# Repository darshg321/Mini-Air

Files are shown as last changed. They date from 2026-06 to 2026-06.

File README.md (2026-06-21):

# Mini-Air

Mini-Air is a DIY FPV drone!
it features:
- a custom flight controller supporting Betaflight
- an ESC supporting Bluejay firmware
- ELRS protocol
- an analog camera
- GPS

the custom flight controller has an on-board OSD, IMU, Barometer, and SPI Flash

i made this project to learn how flight controllers and drones work, and because i want to fly a cool fpv drone. the project is optimized to support the features of all the latest fpv software available. all components are analog to reduce latency, and because 480p drone video with osd in general is really aesthetic. with a 2s lipo and a 2-inch propellers, it leans heavily towards speed rather than range or flight time. the vtx, gps, reciever, and esc are all modular, and so can be swapped with different parts if needed. note that the CAD is simplified to just show the rough connection, i am using a bought frame which will allow for screwing in components.

## Poster (Zine)
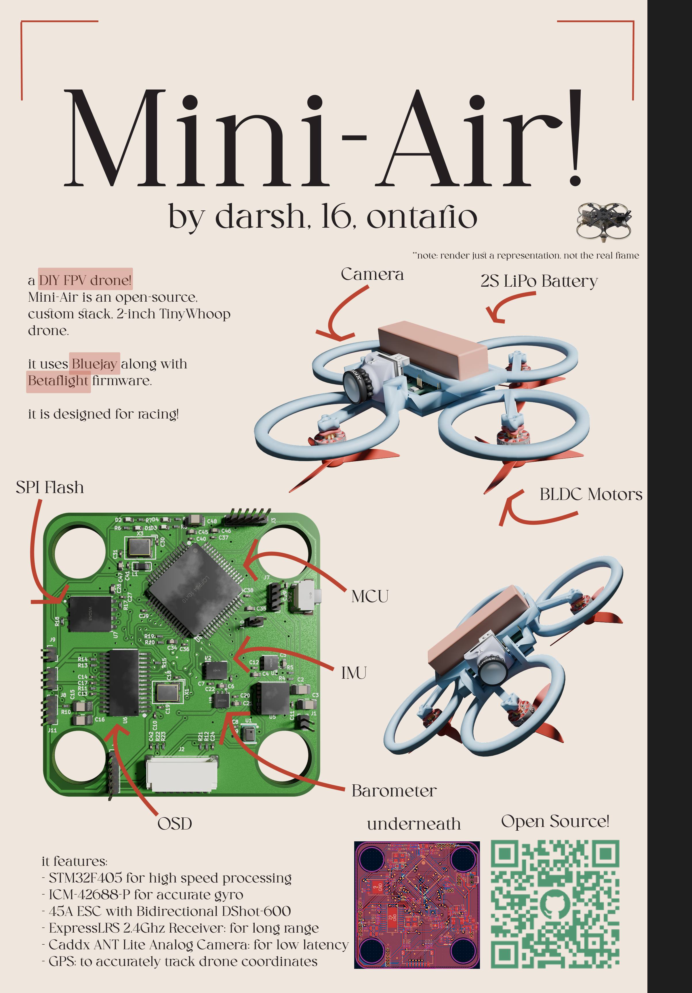
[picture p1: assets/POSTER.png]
poster


## Flight Controller Render
pcb render

## CAD Render
cad render

## PCB
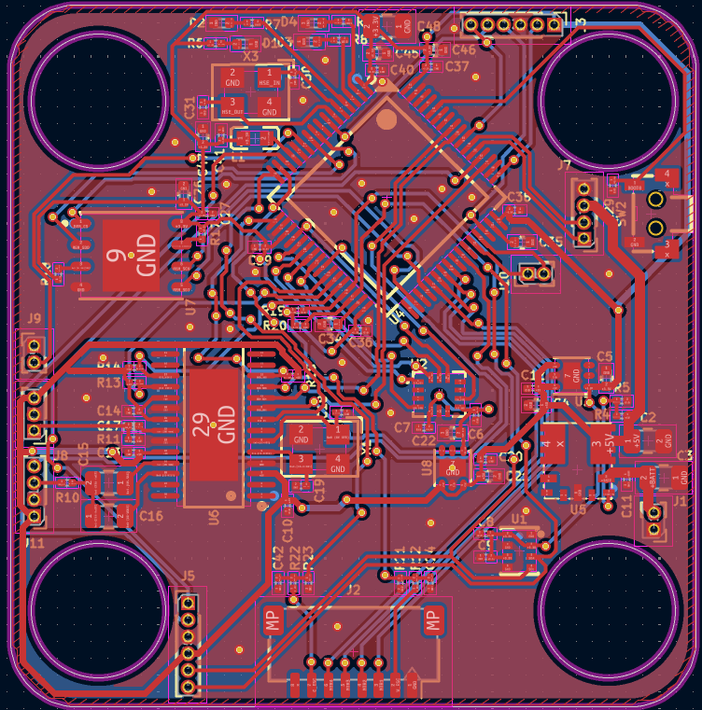
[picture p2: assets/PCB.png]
pcb


## Schematic
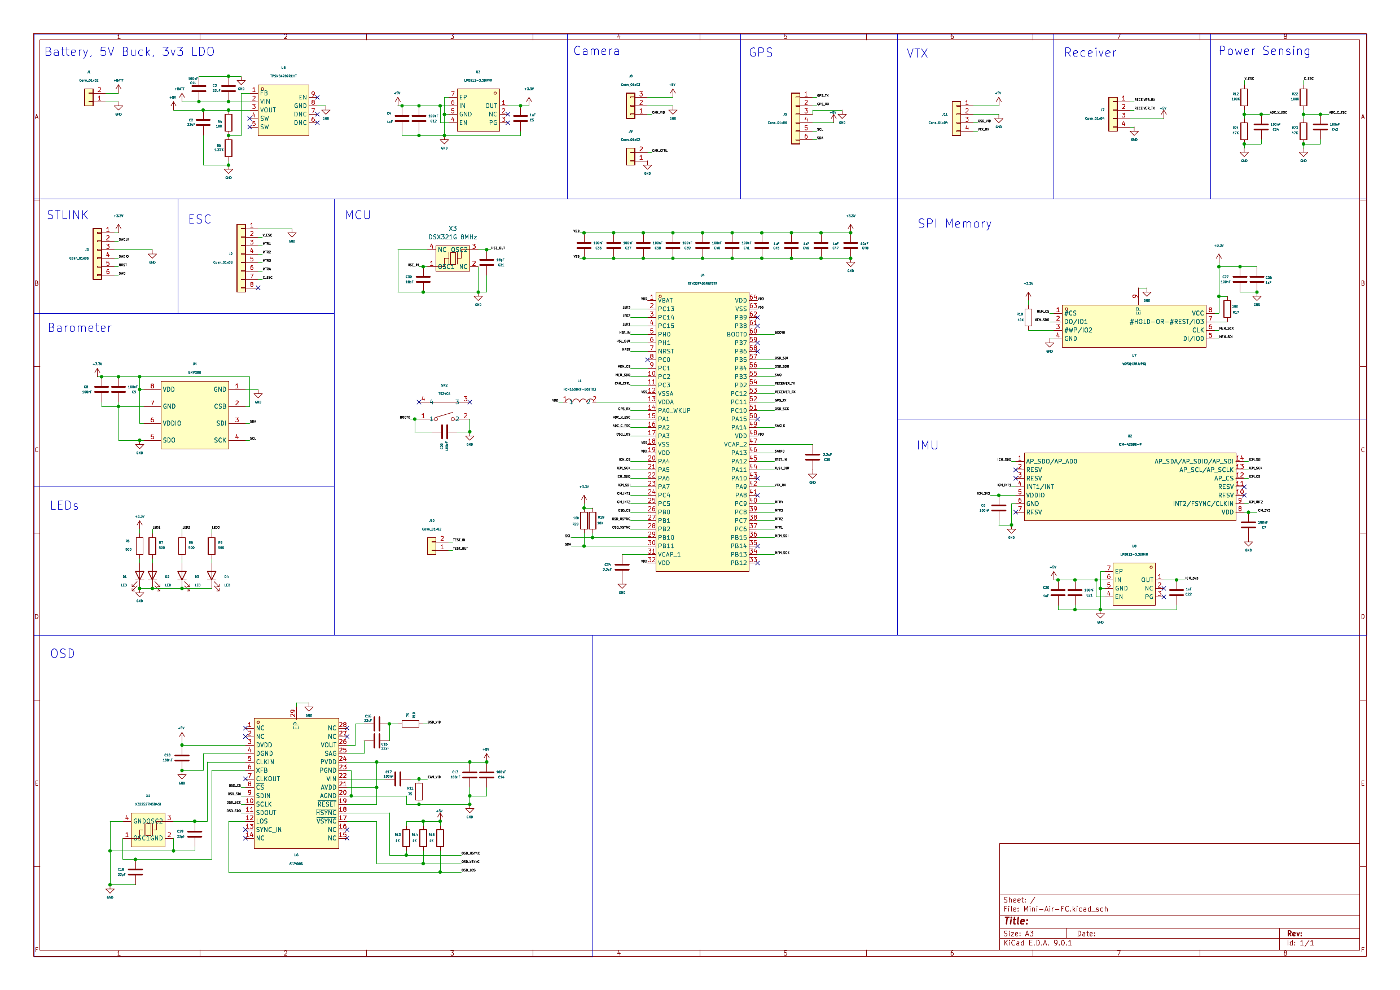
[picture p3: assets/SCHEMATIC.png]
schematic


## CAD
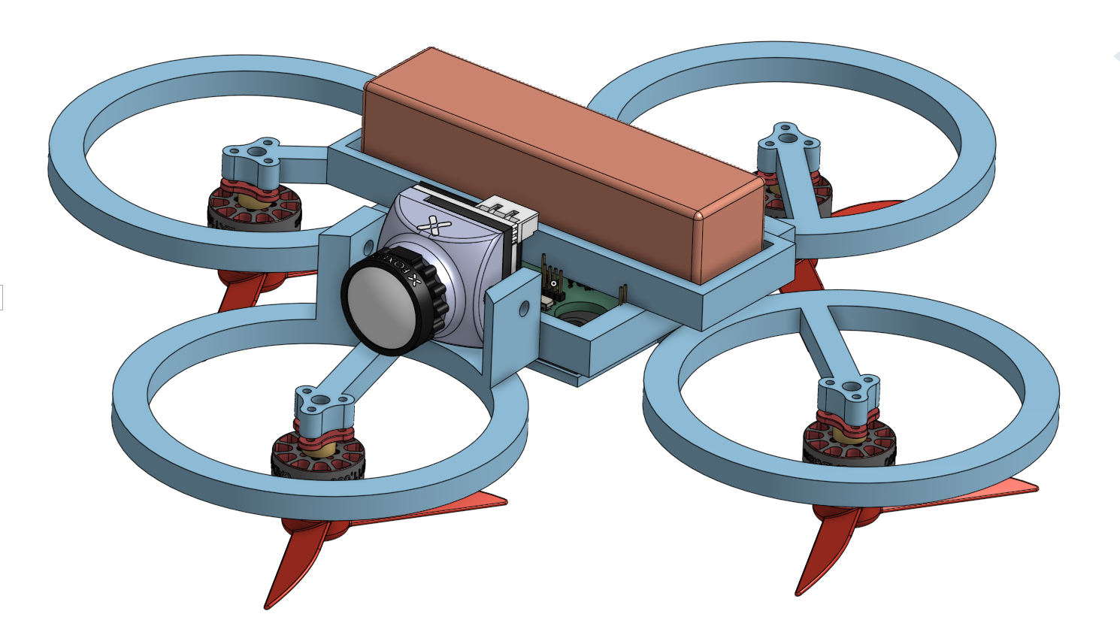
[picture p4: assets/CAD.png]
cad

https://cad.onshape.com/documents/986fb99af7814b930792b89c/w/8ba981f62ca8b18288746bfa/e/dd69b1ef7cccc17bc086fed8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

## Assembly:

1. mount ESC and FC to frame and screw in
2. mount propeller to motor and screw in to frame
3. solder camera, vtx, gps, reciever to flight controller
4. mount camera to front of frame, screw in other components to the back
5. flash betaflight firmware by connecting to FC with a STLINK
6. connect battery and radio controller
7. fly!

## BOM

|Item: |Link: |Price (CAD):|FIELD4|FIELD5 |Weight (g)|
|---|---|---|---|---|---|
|FC PCB | |2.83 | | |3.9 |
|FC PCBA | |236.5 | | | |
|Frame |https://epicfpv.ca/products/hglrc-talon-frame-black |45.31 | | |46 |
|AneegFpv 45A ESC |https://www.aliexpress.com/item/1005009952151526.html |32.99 | | |13 |
|4x HappyModel EX1103S 1103 7000KV |https://www.aliexpress.com/item/1005006105578345.html |44.59 | | |15.2 |
|Propellers |https://www.aliexpress.com/item/1005006966517627.html |6.49 | | |3.52 |
|CADDX Ant FPV Lite Camera |https://www.aliexpress.com/item/1005009014299964.html |19.87 | | |2 |
|Zeus nano 350mW VTX |https://www.aliexpress.com/item/1005008558004179.html |35.58 | | |2.4 |
|Foxeer Lollipop 3 Micro Omni V4 RHCP Antenna|https://www.aliexpress.com/item/4001191873858.html |16.89 | | |4.7 |
|HappyModel 2.4G ELRS EP2 Reciever |https://www.aliexpress.com/item/1005009851731060.html |19.18 | | |0.41 |
|NewBeeDrone M10Q Micro GPS Module |https://newbeedrone.com/products/newbeedrone-m10q-micro-gps-module-with-compass|27.80 | | |2.61 |
|LiteRadio 2 ELRS |https://www.aliexpress.com/item/1005011890268150.html |31.18 | | | |
|x4 2S 450mAh 80C lipo battery |https://www.aliexpress.com/item/1005006138925891.html |37.99 | | |30 |
| | | | | | |
| |Total USD |401.18 | |Weight:|123.74 |

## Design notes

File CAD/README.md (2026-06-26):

**note**: the cad is NOT a frame but rather just a representation of kinda what the drone will look like. the real frame is in the BOM

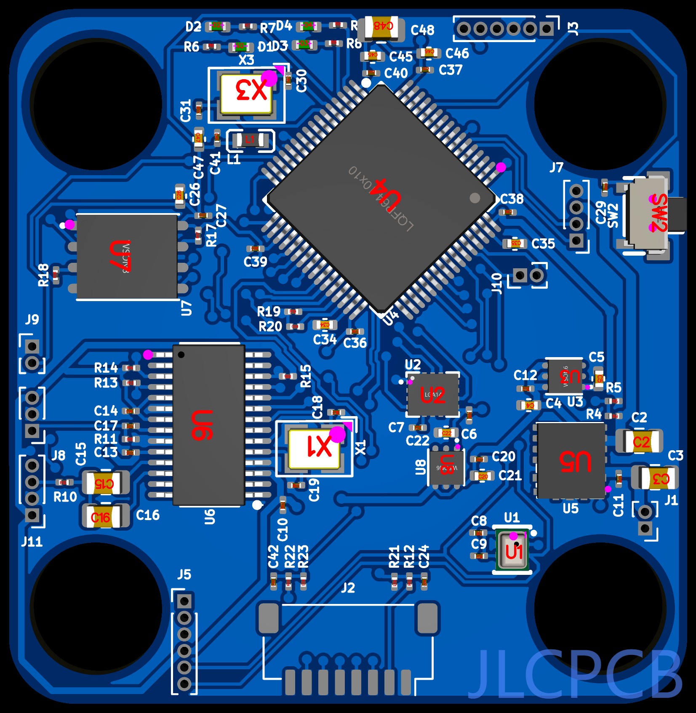
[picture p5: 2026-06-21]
assets/PCB_JLC.png

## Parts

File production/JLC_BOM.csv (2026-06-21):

JLCPCB BOM Tool - BOM Matching
BOM name：production_bom-JLCPCB Assembly Order.xlsx |  |  | Download Time：2026-06-21 03:50:59 |  |  |  | * Our matching results are updated in real-time, but stock and prices may change. If it's been over 24 hours, please re-match before placing your order.
PCB Assembled Qty：5 |  |  | Est. Total Price：83.5555
Your BOM |  |  |  |  | Matched Parts |  |  |  |  |  |  | Order Information
Top Designator | Bottom Designator | Comment | Footprint | JLCPCB Part # | Matches | Part # | Manufacturer | Footprint | Description | Category | Warning | JLCPCB Part # | Product link | Lib Type | Qty | Source | Total Price ($)
C10,C11,C12,C13,C14,C17,C21,C24,C27,C29,C36,C37,C38,C39,C40,C41,C42,C6,C7,C8,C9 |  | 100nF | 0201 |  | Select by Customer | GRM033R61E104KE14D | Murata Electronics | 0201 | 100nF 25V X5R ±10% 0201 Multilayer Ceramic Capacitors MLCC - SMD/SMT ROHS | Multilayer Ceramic Capacitors MLCC - SMD/SMT |  | C76939 | https://jlcpcb.com/partdetail/MurataElectronics-GRM033R61E104KE14D/C76939 | Extended | 54 | 54 JLCPCB | 0.6102
C15,C16,C2,C3 |  | 22uF | 0805 |  | Select by System | CL21A226MAQNNNE | Samsung Electro-Mechanics | 0805 | 22uF 25V X5R ±20% 0805 Multilayer Ceramic Capacitors MLCC - SMD/SMT ROHS | Multilayer Ceramic Capacitors MLCC - SMD/SMT |  | C45783 | https://jlcpcb.com/partdetail/46786-CL21A226MAQNNNE/C45783 | Basic | 16 | 16 JLCPCB | 1.8784
C18,C19 |  | 22pF | 0201 |  | Select by Customer | GRM0335C1H220JA01D | Murata Electronics | 0201 | 22pF 50V C0G ±5% 0201 Multilayer Ceramic Capacitors MLCC - SMD/SMT ROHS | Multilayer Ceramic Capacitors MLCC - SMD/SMT |  | C76924 | https://jlcpcb.com/partdetail/MurataElectronics-GRM0335C1H220JA01D/C76924 | Extended | 20 | 20 JLCPCB | 0.066
C20,C22,C26,C4,C45,C46,C47,C5 |  | 1uF | 0402 |  | Select by System | CL05A105KA5NQNC | Samsung Electro-Mechanics | 0402 | 1uF 25V X5R ±10% 0402 Multilayer Ceramic Capacitors MLCC - SMD/SMT ROHS | Multilayer Ceramic Capacitors MLCC - SMD/SMT |  | C52923 | https://jlcpcb.com/partdetail/53938-CL05A105KA5NQNC/C52923 | Basic | 26 | 26 JLCPCB | 0.4056
C30,C31 |  | 18pF | 0201 |  | Select by System | 0201CG180J500NT | FH (Guangdong Fenghua Advanced Tech) | 0201 | 18pF 50V C0G ±5% 0201 Multilayer Ceramic Capacitors MLCC - SMD/SMT ROHS | Multilayer Ceramic Capacitors MLCC - SMD/SMT |  | C62164 | https://jlcpcb.com/partdetail/63221-0201CG180J500NT/C62164 | Extended | 20 | 20 JLCPCB | 0.028
C34,C35 |  | 2.2uF | 0402 |  | Select by Customer | GRM155R61E225ME15D | Murata Electronics | 0402 | 2.2uF 25V X5R ±20% 0402 Multilayer Ceramic Capacitors MLCC - SMD/SMT ROHS | Multilayer Ceramic Capacitors MLCC - SMD/SMT |  | C72203 | https://jlcpcb.com/partdetail/MurataElectronics-GRM155R61E225ME15D/C72203 | Extended | 8 | 8 JLCPCB | 0.3792
C48 |  | 10uF | 0805 |  | Select by System | GRM21BR61H106KE43L | Murata Electronics | 0805 | 10uF 50V X5R ±10% 0805 Multilayer Ceramic Capacitors MLCC - SMD/SMT ROHS | Multilayer Ceramic Capacitors MLCC - SMD/SMT |  | C440198 | https://jlcpcb.com/partdetail/439567-GRM21BR61H106KE43L/C440198 | Basic | 5 | 5 JLCPCB | 1.053
D1,D2,D3,D4 |  | LED | 0402 |  | Select by Customer | XL-1005UGC | XINGLIGHT | 0402 | -40℃~+85℃ 120° 249mcd 25mA 3V 516nm~531nm 531nm 80mW Discrete Diode Emerald Green Top-mount Water Clear 0402 LED Indication - Discrete ROHS | LED Indication - Discrete | 1.The comment (XL-1005UGC) of this part does not match the one (LED) provided in your BOM. Please confirm; | C965793 | https://jlcpcb.com/partdetail/XINGLIGHT-XL1005UGC/C965793 | Extended | 20 | 20 JLCPCB | 0.16
L1 |  | FCM1608KF-601T03 | L0603 |  | Select by System | FCM1608KF-601T03 | TAI-TECH | 0603 | -55℃~+125℃ 1 350mA 500mΩ 600Ω@100MHz ±25% 0603 Ferrite Beads ROHS | Ferrite Beads |  | C141723 | https://jlcpcb.com/partdetail/TAITECH-FCM1608KF601T03/C141723 | Extended | 20 | 20 JLCPCB | 0.202
R5 |  | 1.37K | 0201 |  | Select by Customer | RTT011371FTH | RALEC | 0201 | -55℃~+125℃ 1.37kΩ 25V 50mW Thick Film Resistor ±1% ±200ppm/℃ 0201 Chip Resistor - Surface Mount ROHS | Chip Resistor - Surface Mount | 1.The comment (RTT011371FTH) of this part does not match the one (1.37K) provided in your BOM. Please confirm; | C166356 | https://jlcpcb.com/partdetail/RALEC-RTT011371FTH/C166356 | Extended | 20 | 20 JLCPCB | 0.028
R6,R7,R8,R9 |  | 500 | 0201 |  | Select by Customer | RC0201FR-07499RL | YAGEO | 0201 | -55℃~+125℃ 25V 499Ω 50mW Thick Film Resistor ±1% ±200ppm/℃ 0201 Chip Resistor - Surface Mount ROHS | Chip Resistor - Surface Mount | 1.The comment (RC0201FR-07499RL) of this part does not match the one (500) provided in your BOM. Please confirm; | C138137 | https://jlcpcb.com/partdetail/YAGEO-RC0201FR07499RL/C138137 | Extended | 20 | 20 JLCPCB | 0.022
R10,R11 |  | 75 | 0201 |  | Select by Customer | AC0201FR-0775RL | YAGEO | 0201 | -55℃~+155℃ 25V 50mW 75Ω Thick Film Resistor ±1% ±200ppm/℃ 0201 Chip Resistor - Surface Mount ROHS | Chip Resistor - Surface Mount | 1.The comment (AC0201FR-0775RL) of this part does not match the one (75) provided in your BOM. Please confirm; | C226616 | https://jlcpcb.com/partdetail/YAGEO-AC0201FR0775RL/C226616 | Extended | 20 | 20 JLCPCB | 0.04
R12,R22 |  | 100K | 0201 |  | Select by Customer | RTT011003FTH | RALEC | 0201 | -55℃~+125℃ 100kΩ 25V 50mW Thick Film Resistor ±1% ±200ppm/℃ 0201 Chip Resistor - Surface Mount ROHS | Chip Resistor - Surface Mount | 1.The comment (RTT011003FTH) of this part does not match the one (100K) provided in your BOM. Please confirm; | C102685 | https://jlcpcb.com/partdetail/RALEC-RTT011003FTH/C102685 | Extended | 20 | 20 JLCPCB | 0.02
R13,R14,R15 |  | 1K | 0201 |  | Select by Customer | RC0201FR-071KL | YAGEO | 0201 | -55℃~+125℃ 1kΩ 25V 50mW Thick Film Resistor ±1% ±200ppm/℃ 0201 Chip Resistor - Surface Mount ROHS | Chip Resistor - Surface Mount | 1.The comment (RC0201FR-071KL) of this part does not match the one (1K) provided in your BOM. Please confirm; | C138165 | https://jlcpcb.com/partdetail/YAGEO-RC0201FR071KL/C138165 | Extended | 20 | 20 JLCPCB | 0.022
R17,R18,R19,R20,R4 |  | 10K | 0201 |  | Select by Customer | RC0201JR-0710KL | YAGEO | 0201 | -55℃~+125℃ 10kΩ 25V 50mW Thick Film Resistor ±200ppm/℃ ±5% 0201 Chip Resistor - Surface Mount ROHS | Chip Resistor - Surface Mount | 1.The comment (RC0201JR-0710KL) of this part does not match the one (10K) provided in your BOM. Please confirm; | C138117 | https://jlcpcb.com/partdetail/YAGEO-RC0201JR0710KL/C138117 | Extended | 20 | 20 JLCPCB | 0.02
R21,R23 |  | 47K | 0201 |  | Select by Customer | RC0201FR-0747KL | YAGEO | 0201 | -55℃~+125℃ 25V 47kΩ 50mW Thick Film Resistor ±1% ±200ppm/℃ 0201 Chip Resistor - Surface Mount ROHS | Chip Resistor - Surface Mount | 1.The comment (RC0201FR-0747KL) of this part does not match the one (47K) provided in your BOM. Please confirm; | C138139 | https://jlcpcb.com/partdetail/YAGEO-RC0201FR0747KL/C138139 | Extended | 20 | 20 JLCPCB | 0.022
SW2 |  | TS24CA | SW-SMD_2P-TS24CA |  | Select by System | TS24CA | SHOU HAN | SMD,4.6x1.8mm | -20℃~+70℃ 1.6N 1.9mm 12V 20,000 cycles 3.5mm 4.7mm 50mA Black No Rectangular Button SMD(SMT) Tab SPST Surface Mount, Right Angle Without Bracket SMD,4.6x1.8mm Tactile Switches ROHS | Tactile Switches |  | C393942 | https://jlcpcb.com/partdetail/SHOUHAN-TS24CA/C393942 | Extended | 7 | 7 JLCPCB | 0.175
U1 |  | BMP280 | LGA-8_L2.5-W2.0-P0.65_AMP6127 |  | Select by System | BMP280 | Bosch Sensortec | LGA-8(2x2.5) | -40℃~+85℃ 0.12hpa 1.5pa/K 1.71V~3.6V 1hpa 300nA 30Kpa~1.1bar I2C、SPI LGA-8(2x2.5) Pressure Sensors ROHS | Pressure Sensors |  | C83291 | https://jlcpcb.com/partdetail/BoschSensortec-BMP280/C83291 | Extended | 2 | 2 JLCPCB | 13.7058
U2 |  | ICM-42688-P | LGA-14_L3.0-W2.5-P0.50-TL |  | Select by System | ICM-42688-P | TDK InvenSense | LGA-14(2.5x3) | -40℃~+85℃ 1.71V~3.6V 16bit 2KB 7.5uA IMU (accelerometer + gyroscope) SPI、I2C X,Y,Z X,Y,Z ±16g ±2000dps Motion Event Detection, Synchronization, Timestamp Support LGA-14(2.5x3) Accelerometers ROHS | Accelerometers |  | C1850418 | https://jlcpcb.com/partdetail/TDKInvenSense-ICM_42688P/C1850418 | Extended | 2 | 2 JLCPCB | 28.359
U3,U8 |  | LP5912-3.3DRVR | WSON-6_L2.0-W2.0-P0.65-TL-EP |  | Select by System | LP5912-3.3DRVR | Texas Instruments | WSON-6-EP(2x2) | -40℃~+125℃@(Tj) 1 12uVrms 180mV@(500mA) 3.3V 30uA 500mA 6.5V 75dB@(1kHz) Fixed Over Temperature Protection、Reverse connection protection、Soft Start、Short Circuit Protection Positive WSON-6-EP(2x2) Voltage Regulators - Linear, Low Drop Out (LDO) Regulators ROHS | Voltage Regulators - Linear, Low Drop Out (LDO) Regulators |  | C524780 | https://jlcpcb.com/partdetail/TexasInstruments-LP5912_33DRVR/C524780 | Extended | 4 | 4 JLCPCB | 3.068
U4 |  | STM32F405RGT6TR | LQFP-64_L10.0-W10.0-P0.50-LS12.0-BL |  | Select by System | STM32F405RGT6TR | STMicroelectronics | LQFP-64_10x10 | -40℃~+85℃ 1.8V~3.6V 12bit 12bit 168MHz 192KB 1MB 32 Bit 51 ARM Cortex-M4 Built-in FLASH LQFP-64(10x10) Microcontrollers (MCU/MPU/SOC) ROHS | Microcontrollers (MCU/MPU/SOC) |  | C2054141 | https://jlcpcb.com/partdetail/STMicroelectronics-STM32F405RGT6TR/C2054141 | Extended | 2 | 2 JLCPCB | 10.654
U5 |  | TPSM84209RKHT | QFN-9_L4.4-W4.0-P0.85-YTL |  | Select by System | TPSM84209RKHT | Texas Instruments | QFN-9(4x4.4) | -40℃~+85℃ 1 1.2V~6V 2.5A 4.5V~28V 750kHz Adjustable Buck Buck Built-in QFN-9(4x4.4) DC-DC Converters ROHS | DC-DC Converters |  | C2836944 | https://jlcpcb.com/partdetail/TexasInstruments-TPSM84209RKHT/C2836944 | Extended | 2 | 2 JLCPCB | 7.8472
U6 |  | AT7456E | TSSOP-28_L9.7-W4.4-P0.65-LS6.4-BL-EP-2 |  | Select by System | AT7456E | ZHONGKEWEI | TSSOP-28-EP | TSSOP-28-EP Microcontrollers (MCU/MPU/SOC) ROHS | Microcontrollers (MCU/MPU/SOC) |  | C82351 | https://jlcpcb.com/partdetail/ZHONGKEWEI-AT7456E/C82351 | Extended | 2 | 2 JLCPCB | 5.8588
U7 |  | W25Q128JVPIQ | WSON-8_L6.0-W5.0-P1.27-BL-EP |  | Select by System | W25Q128JVPIQ | Winbond Elec | WSON-8-EP(5x6) | -40℃~+85℃ 100,000 cycles 10uA 120ms@(32KB) 128Mbit 133MHz 2.7V~3.6V 20 Years Power-on reset、Hardware write protection、Software write protection、Write enable latch、Absolute write protection、Power lock protection SPI WSON-8-EP(5x6) NOR FLASH ROHS | NOR FLASH |  | C190862 | https://jlcpcb.com/partdetail/WinbondElec-W25Q128JVPIQ/C190862 | Extended | 2 | 2 JLCPCB | 6.7256
X1 |  | X322527MSB4SI | CRYSTAL-SMD_4P-L3.2-W2.5-BL-1 |  | Select by System | X322527MSB4SI | YXC Crystal Oscillators | SMD3225-4P | -40℃~+85℃ 20pF 27MHz Crystal Oscillator ±10ppm ±20ppm SMD3225-4P Crystals ROHS | Crystals |  | C9008 | https://jlcpcb.com/partdetail/YXC_CrystalOscillators-X322527MSB4SI/C9008 | Extended | 6 | 6 JLCPCB | 0.6072
X3 |  | DSX321G8MHz | CRYSTAL-SMD_4P-L3.2-W2.5-BL-1 |  | Select by System | 1C208000BC0R | KDS Daishinku | SMD3225-4P | 12pF 8MHz Crystal Oscillator ±20ppm SMD3225-4P Crystals ROHS | Crystals |  | C57131 | https://jlcpcb.com/partdetail/KDSDaishinku-1C208000BC0R/C57131 | Extended | 5 | 5 JLCPCB | 1.5985
J1,J10,J9 |  | Conn_01x02 | PinHeader_1x02_P1.00mm_Vertical |  | No matches | No Part Selected
J2 |  | Conn_01x08 | JST_SH_SM08B-SRSS-TB_1x08-1MP_P1.00mm_Horizontal |  | No matches | No Part Selected
J3,J5 |  | Conn_01x06 | PinHeader_1x06_P1.00mm_Vertical |  | No matches | No Part Selected
J8 |  | Conn_01x03 | PinHeader_1x03_P1.00mm_Vertical |  | No matches | No Part Selected
J11,J7 |  | Conn_01x04 | PinHeader_1x04_P1.00mm_Vertical |  | No matches | No Part Selected

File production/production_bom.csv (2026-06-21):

Designator | Footprint | Quantity | Value | LCSC Part #
C10, C11, C12, C13, C14, C17, C21, C24, C27, C29, C36, C37, C38, C39, C40, C41, C42, C6, C7, C8, C9 | 0201 | 21 | 100nF
C15, C16, C2, C3 | 0805 | 4 | 22uF
C18, C19 | 0201 | 2 | 22pF
C20, C22, C26, C4, C45, C46, C47, C5 | 0402 | 8 | 1uF
C30, C31 | 0201 | 2 | 18pF
C34, C35 | 0402 | 2 | 2.2uF
C48 | 0805 | 1 | 10uF
D1, D2, D3, D4 | 0402 | 4 | LED
J1, J10, J9 | PinHeader_1x02_P1.00mm_Vertical | 3 | Conn_01x02
J11, J7 | PinHeader_1x04_P1.00mm_Vertical | 2 | Conn_01x04
J2 | JST_SH_SM08B-SRSS-TB_1x08-1MP_P1.00mm_Horizontal | 1 | Conn_01x08
J3, J5 | PinHeader_1x06_P1.00mm_Vertical | 2 | Conn_01x06
J8 | PinHeader_1x03_P1.00mm_Vertical | 1 | Conn_01x03
L1 | L0603 | 1 | FCM1608KF-601T03 | C141723
R10, R11 | 0201 | 2 | 75
R12, R22 | 0201 | 2 | 100K
R13, R14, R15 | 0201 | 3 | 1K
R17, R18, R19, R20, R4 | 0201 | 5 | 10K
R21, R23 | 0201 | 2 | 47K
R5 | 0201 | 1 | 1.37K
R6, R7, R8, R9 | 0201 | 4 | 500
SW2 | SW-SMD_2P-TS24CA | 1 | TS24CA | C393942
U1 | LGA-8_L2.5-W2.0-P0.65_AMP6127 | 1 | BMP280 | C83291
U2 | LGA-14_L3.0-W2.5-P0.50-TL | 1 | ICM-42688-P | C1850418
U3, U8 | WSON-6_L2.0-W2.0-P0.65-TL-EP | 2 | LP5912-3.3DRVR | C524780
U4 | LQFP-64_L10.0-W10.0-P0.50-LS12.0-BL | 1 | STM32F405RGT6TR | C2054141
U5 | QFN-9_L4.4-W4.0-P0.85-YTL | 1 | TPSM84209RKHT | C2836944
U6 | TSSOP-28_L9.7-W4.4-P0.65-LS6.4-BL-EP-2 | 1 | AT7456E | C82351
U7 | WSON-8_L6.0-W5.0-P1.27-BL-EP | 1 | W25Q128JVPIQ | C190862
X1 | CRYSTAL-SMD_4P-L3.2-W2.5-BL-1 | 1 | X322527MSB4SI | C9008
X3 | CRYSTAL-SMD_4P-L3.2-W2.5-BL-1 | 1 | DSX321G 8MHz | C57131

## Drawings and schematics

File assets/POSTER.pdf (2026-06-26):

# Mini-Air!

# by darsh, 16, ontario

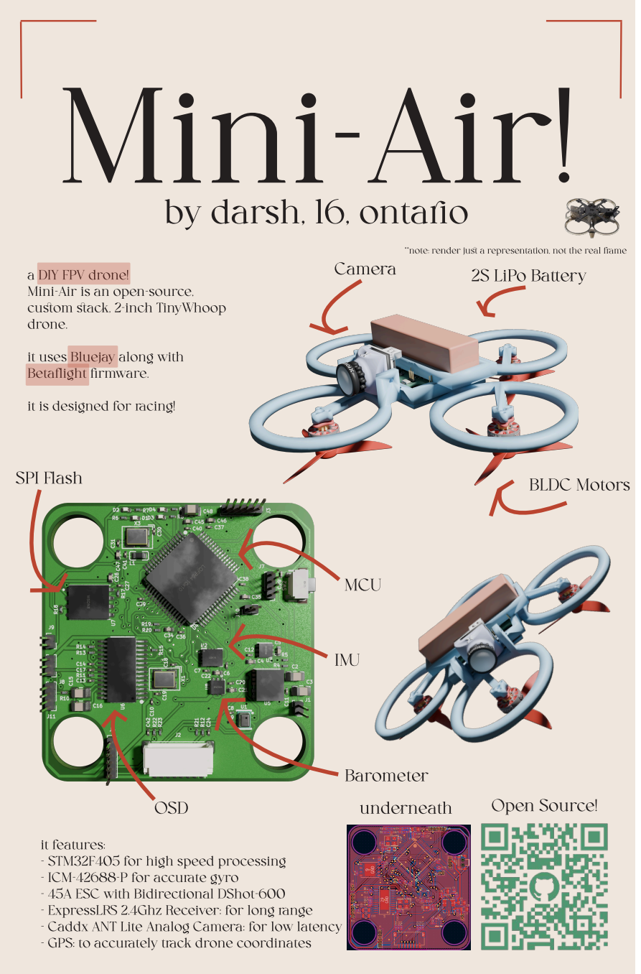
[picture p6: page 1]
drone.; Camera; 2S LiPo Battery; SPI Flash; BLDC Motors; MCU; IMU; OSD; Barometer; underneath; Open Source!; it features:

**note: render just a representation, not the real frame

a DIY FPV drone!

Mini-Air is an open-source,
custom stack, 2-inch TinyWhoop

it uses Bluejay along with
Betaflight firmware.

it is designed for racing!

- STM32F405 for high speed processing

- ICM-42688-P for accurate gyro

- 45A ESC with Bidirectional DShot-600

- ExpressLRS 2.4Ghz Receiver: for long range

- Caddx ANT Lite Analog Camera: for low latency

- GPS: to accurately track drone coordinates

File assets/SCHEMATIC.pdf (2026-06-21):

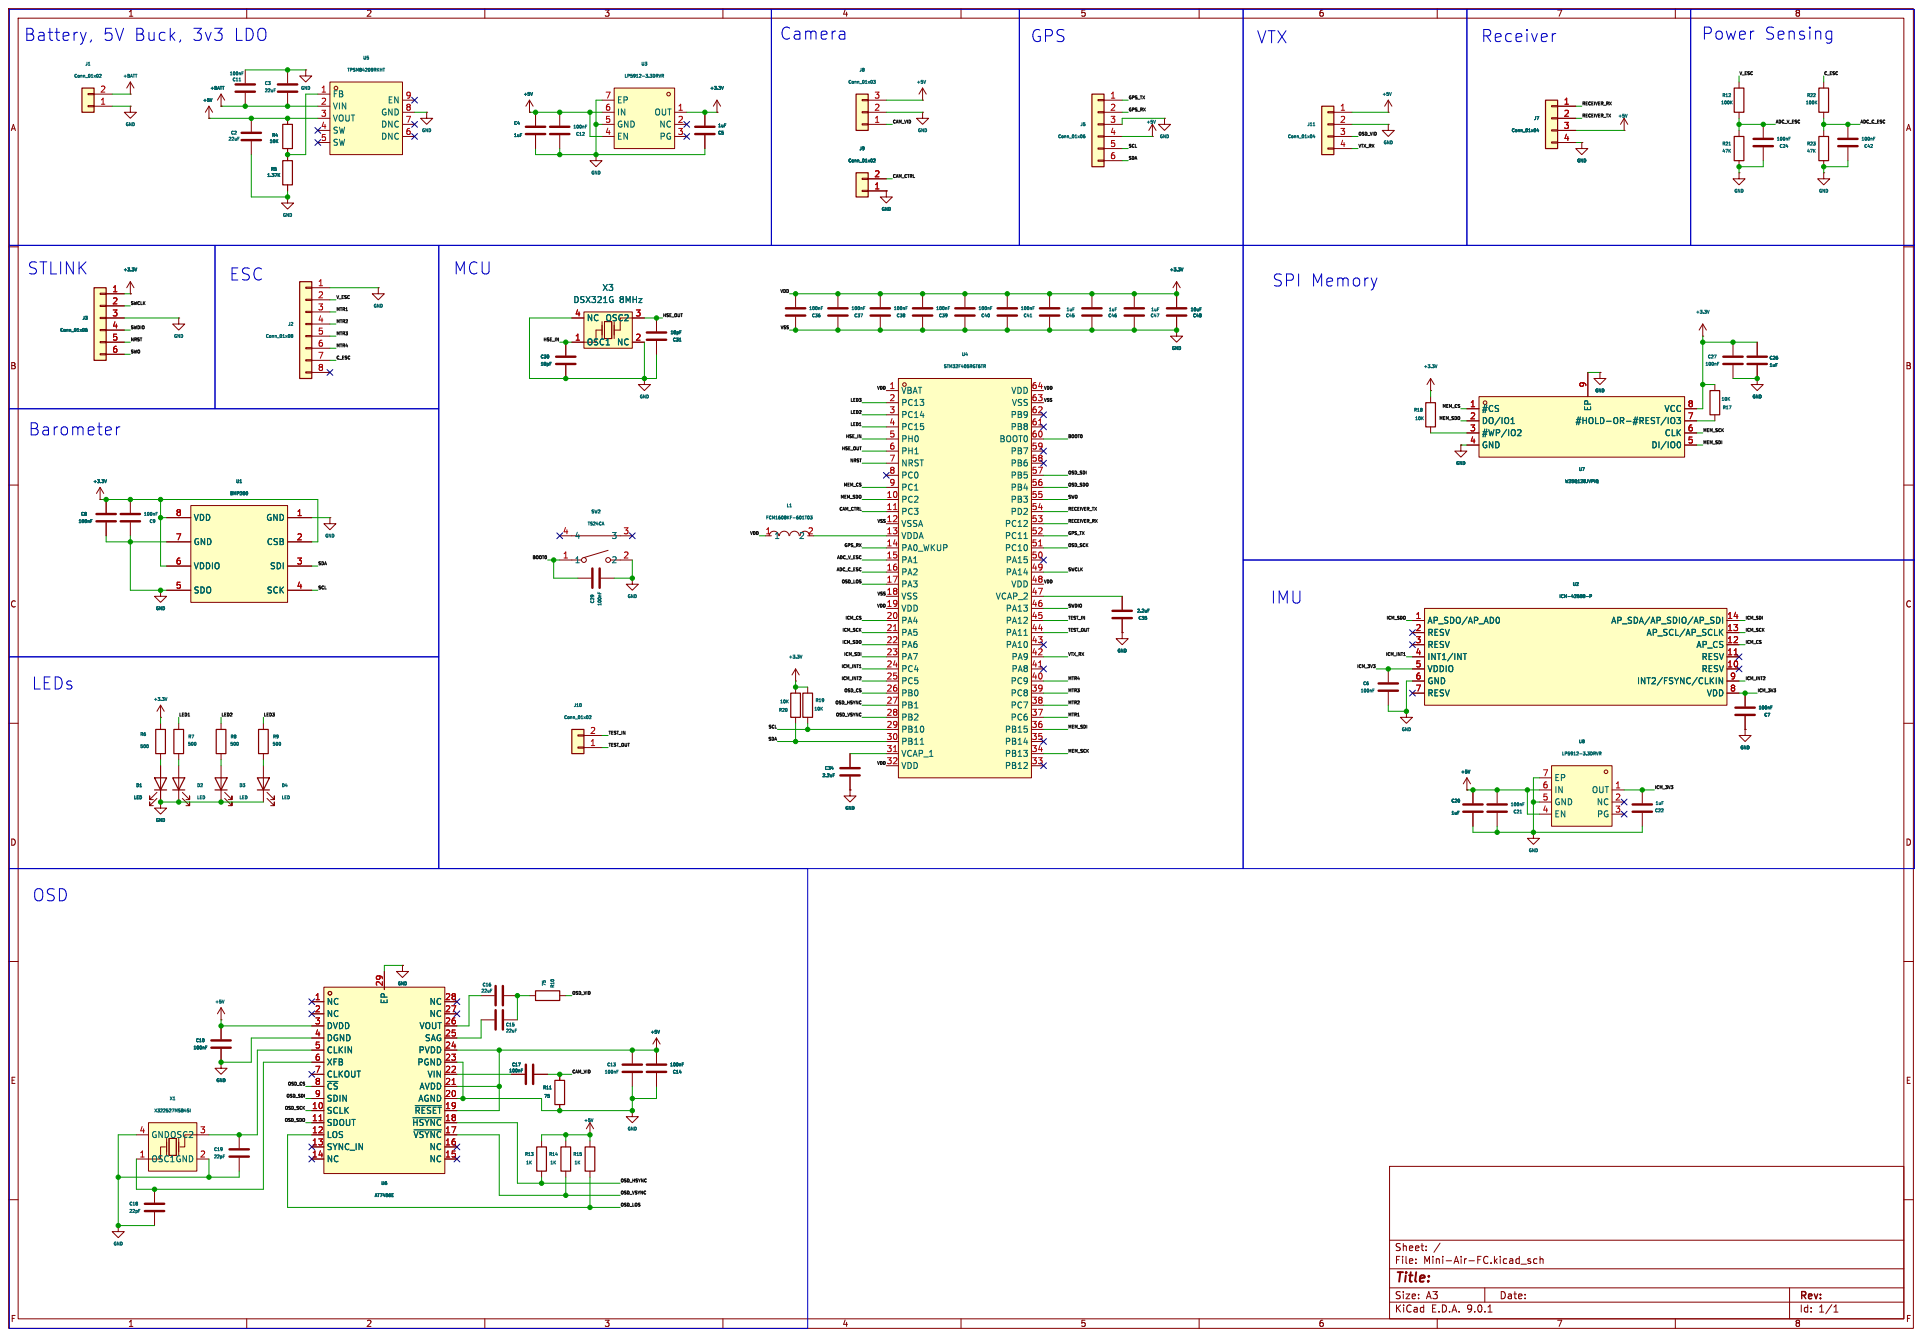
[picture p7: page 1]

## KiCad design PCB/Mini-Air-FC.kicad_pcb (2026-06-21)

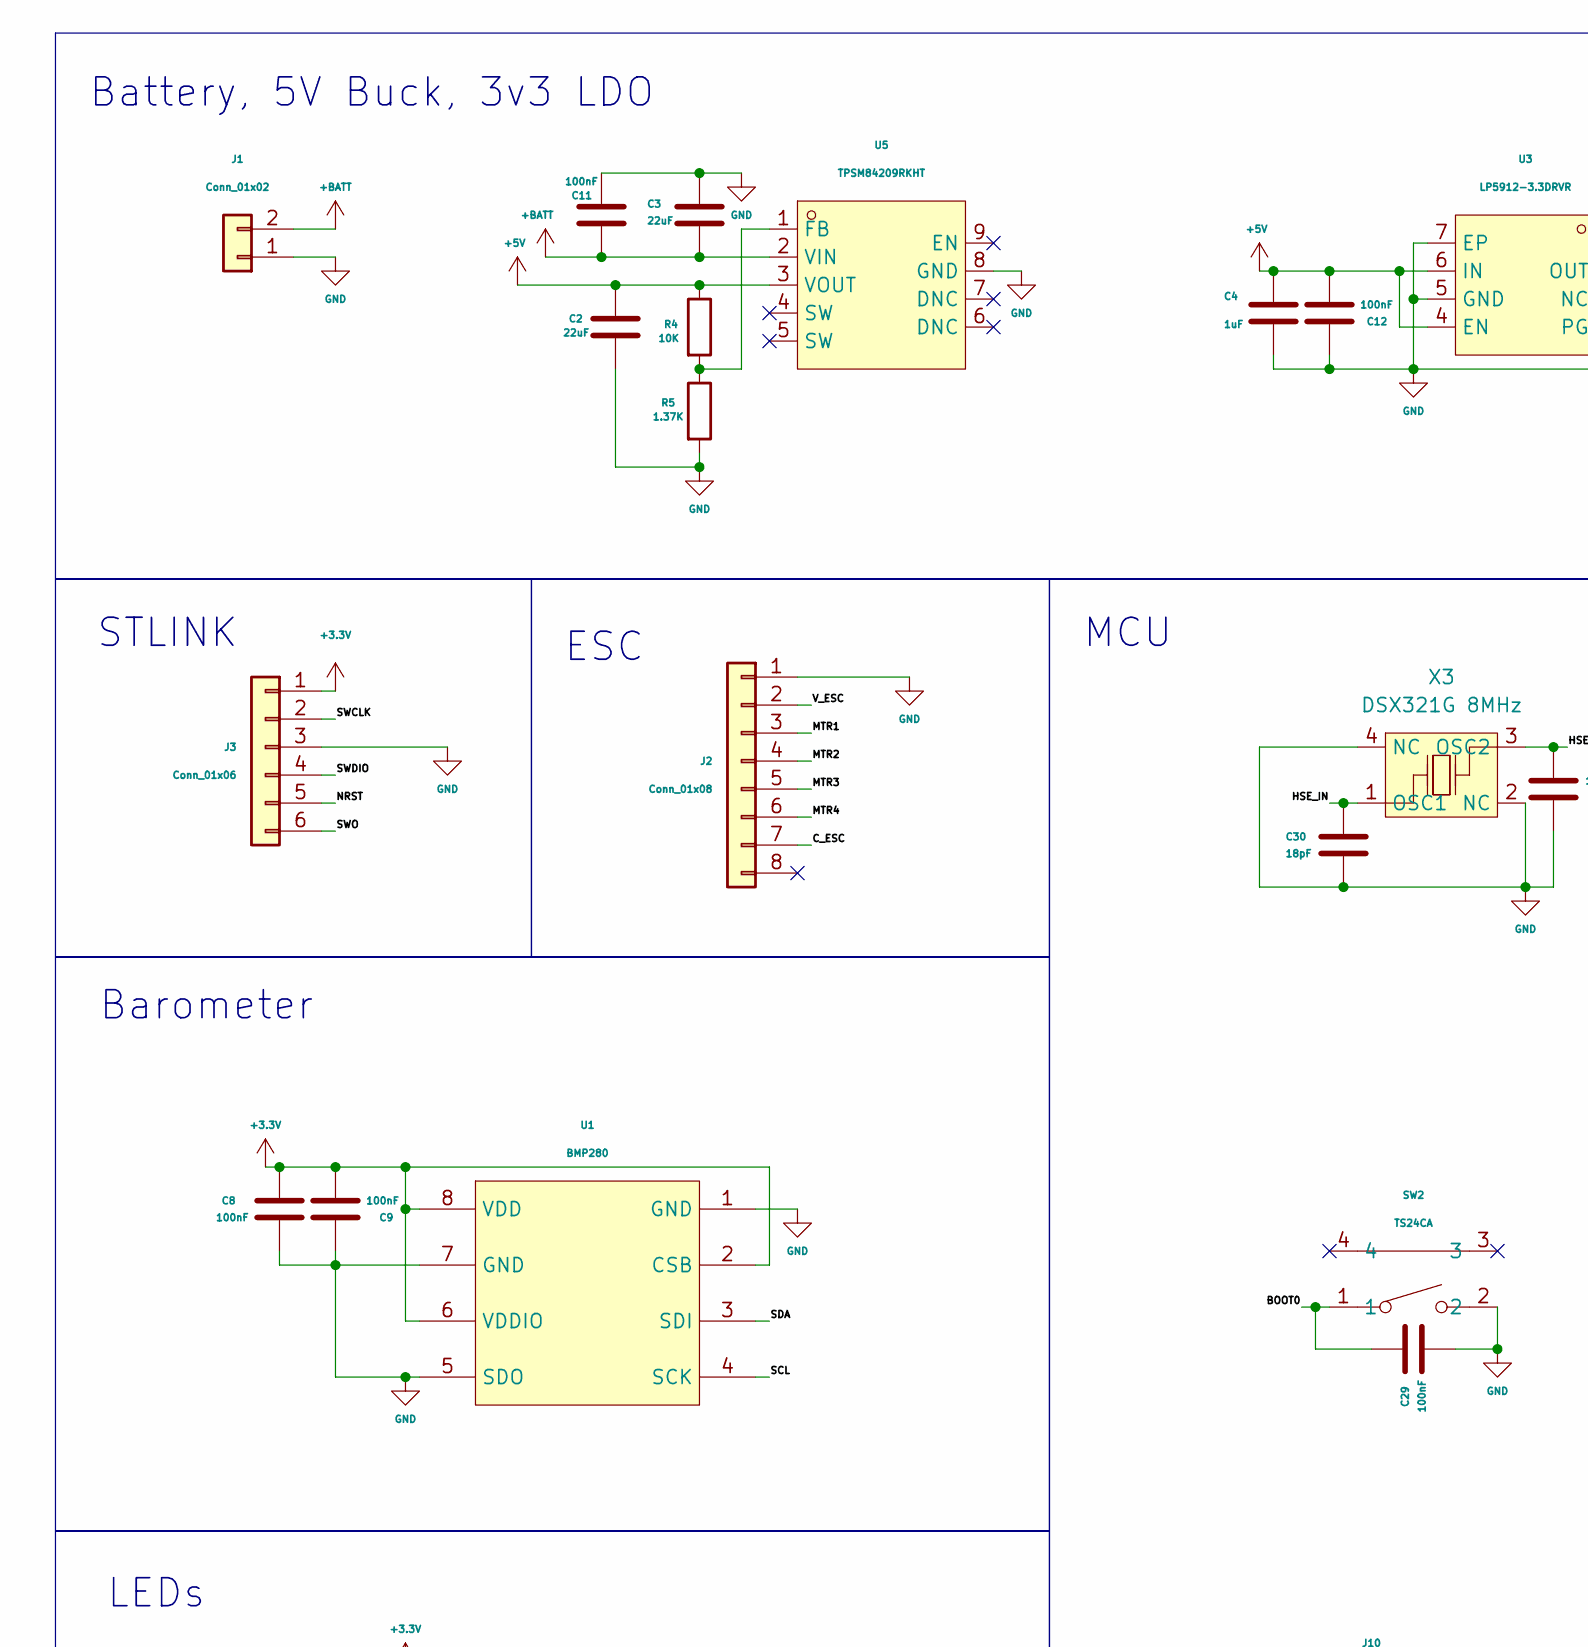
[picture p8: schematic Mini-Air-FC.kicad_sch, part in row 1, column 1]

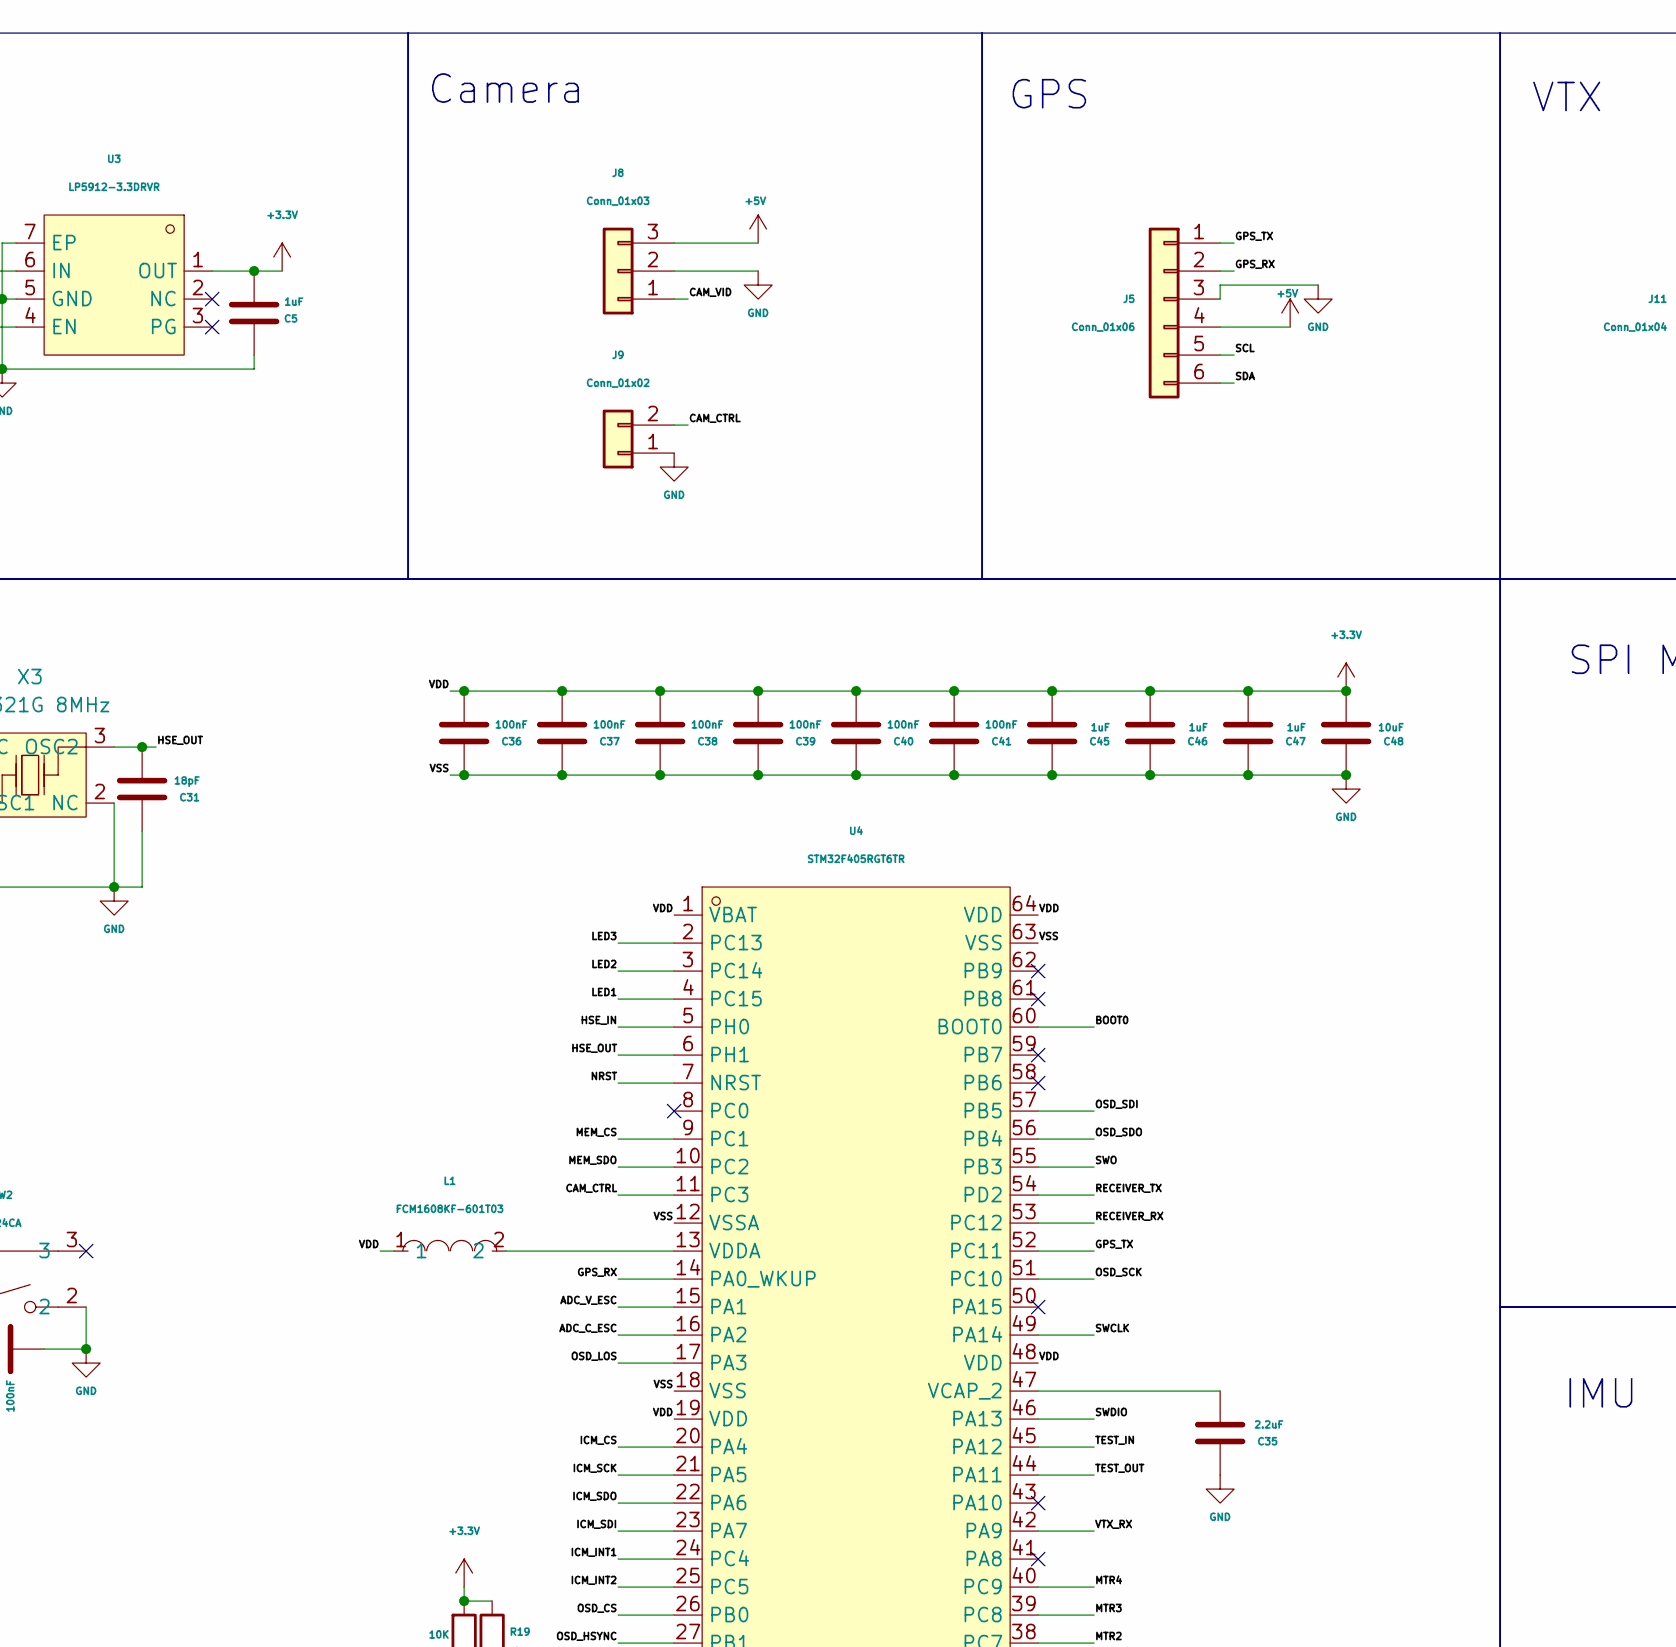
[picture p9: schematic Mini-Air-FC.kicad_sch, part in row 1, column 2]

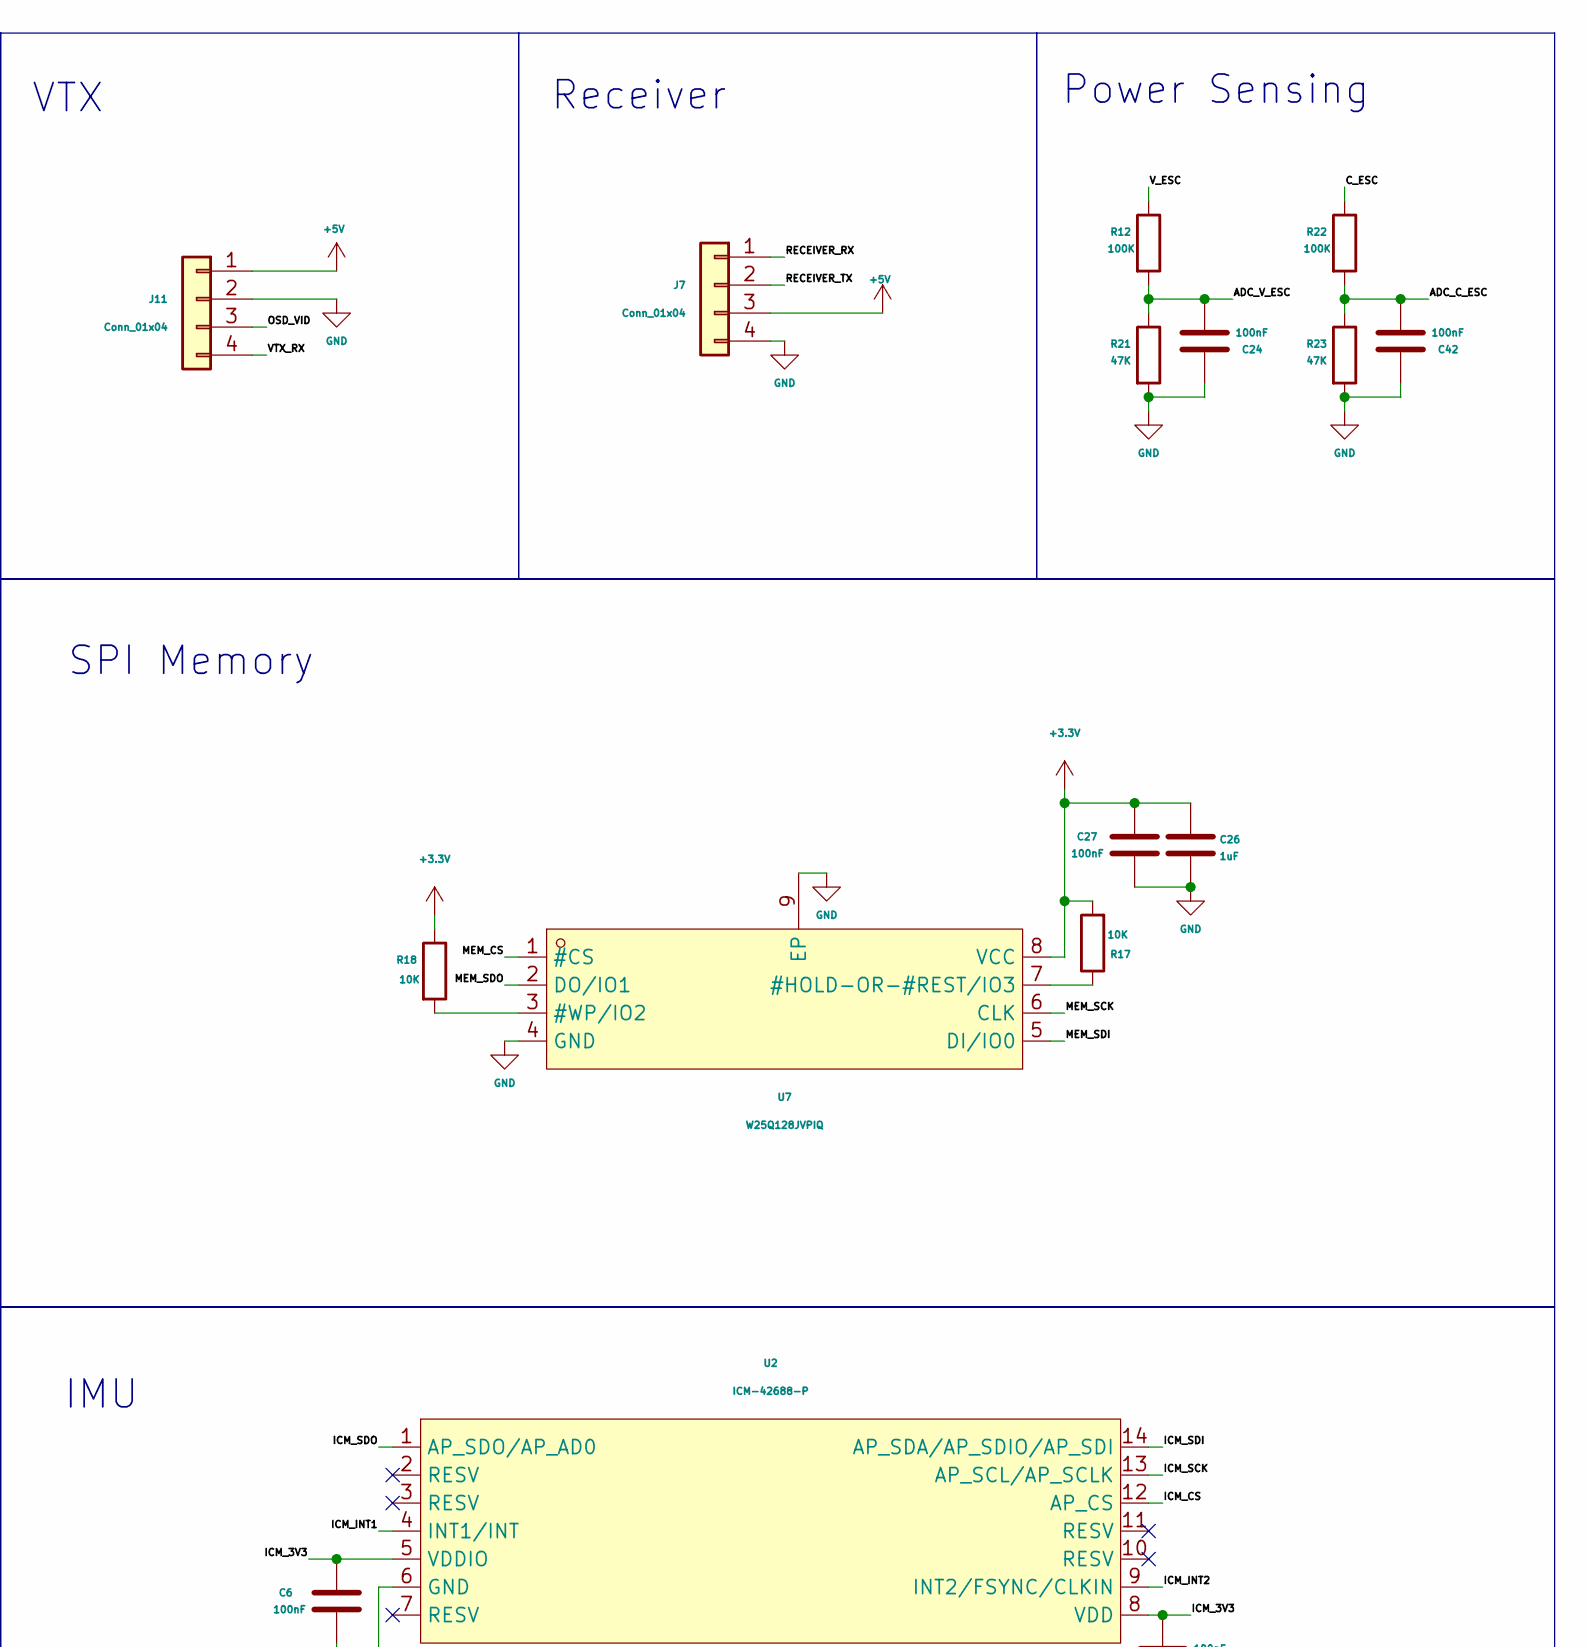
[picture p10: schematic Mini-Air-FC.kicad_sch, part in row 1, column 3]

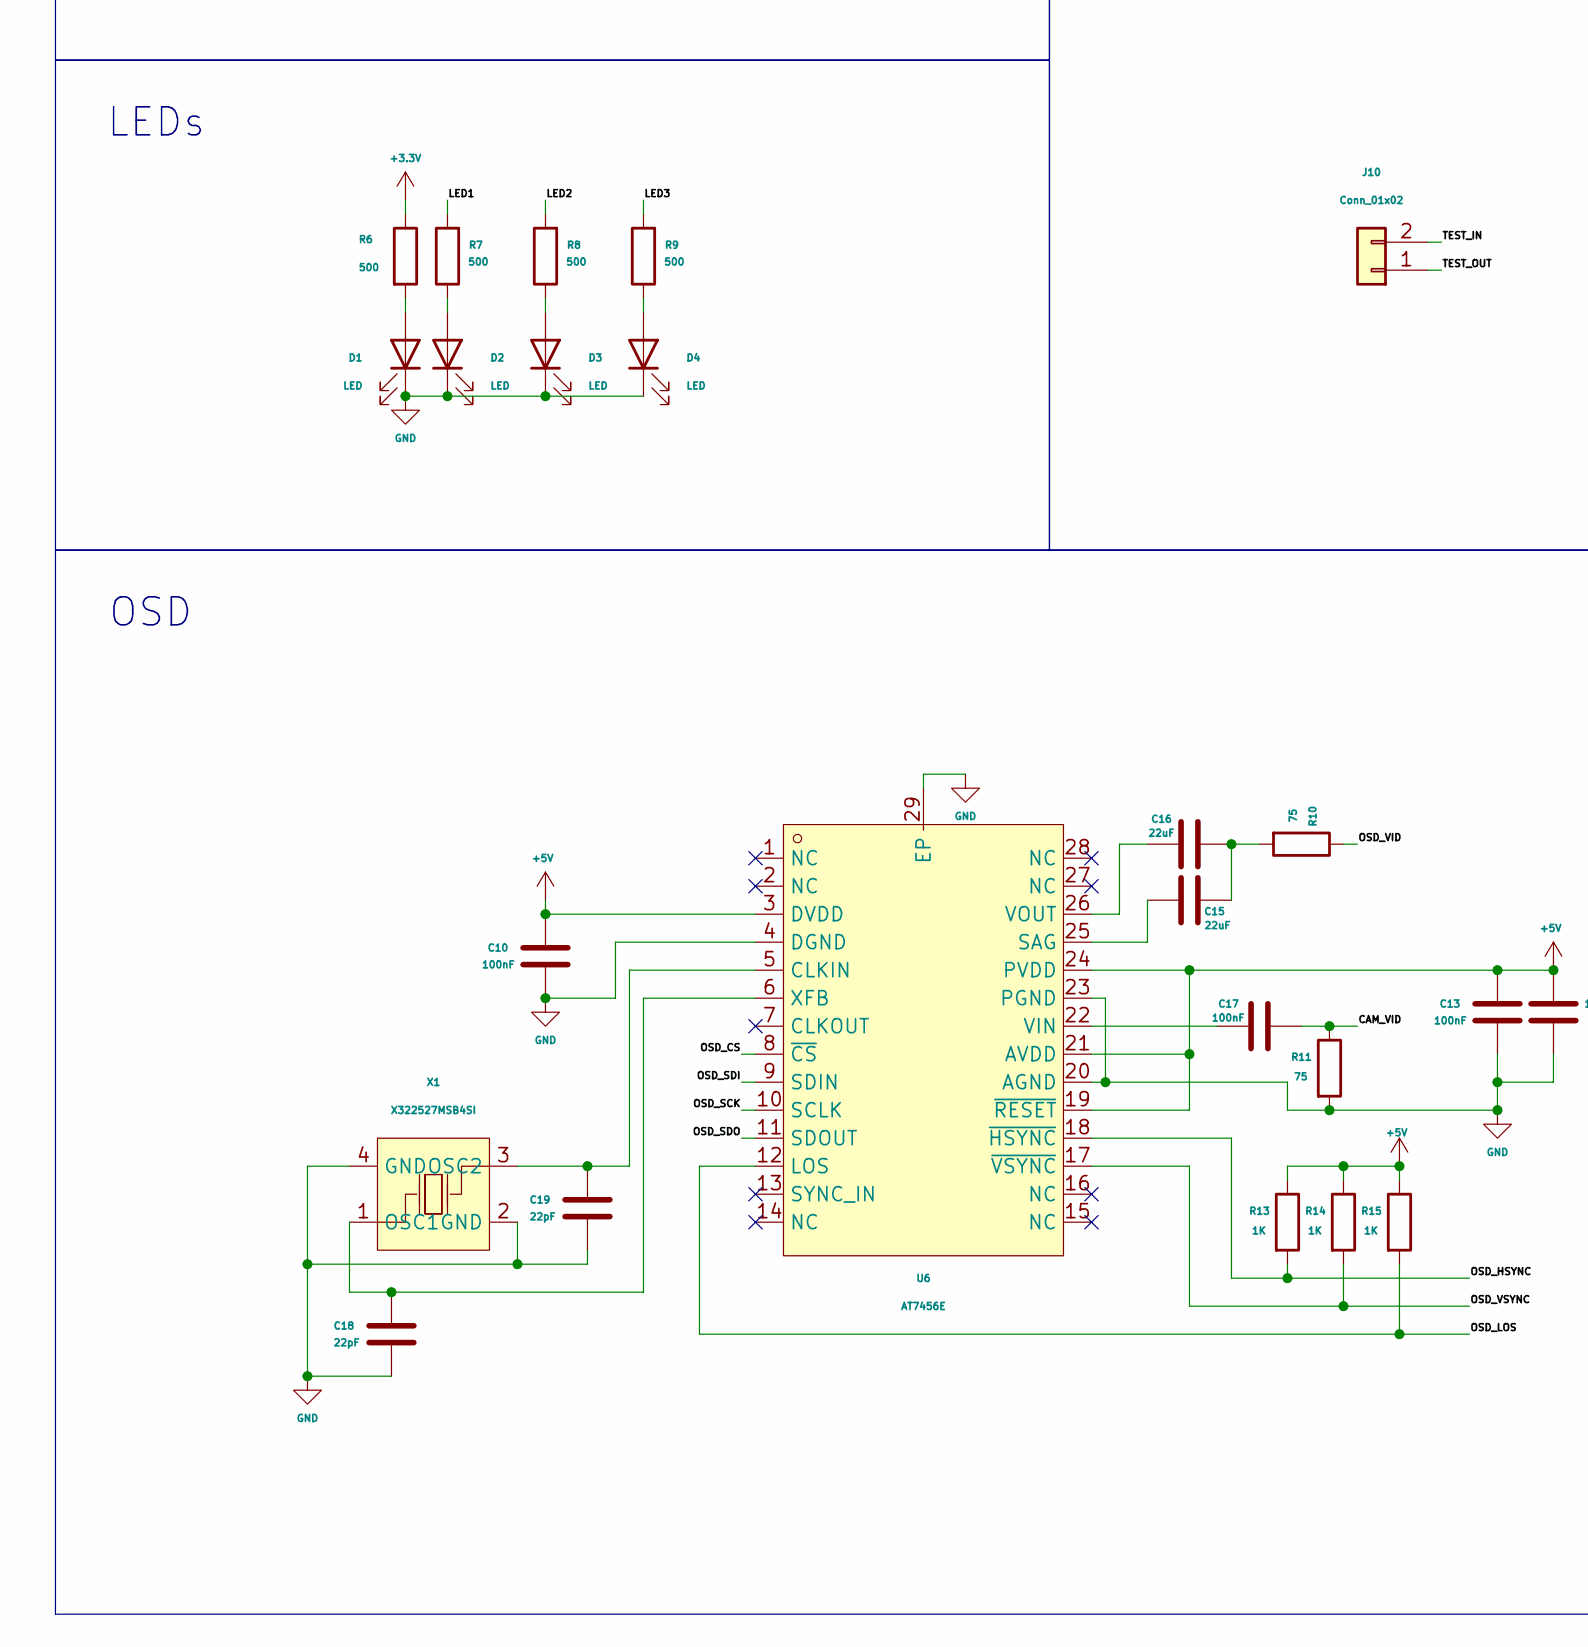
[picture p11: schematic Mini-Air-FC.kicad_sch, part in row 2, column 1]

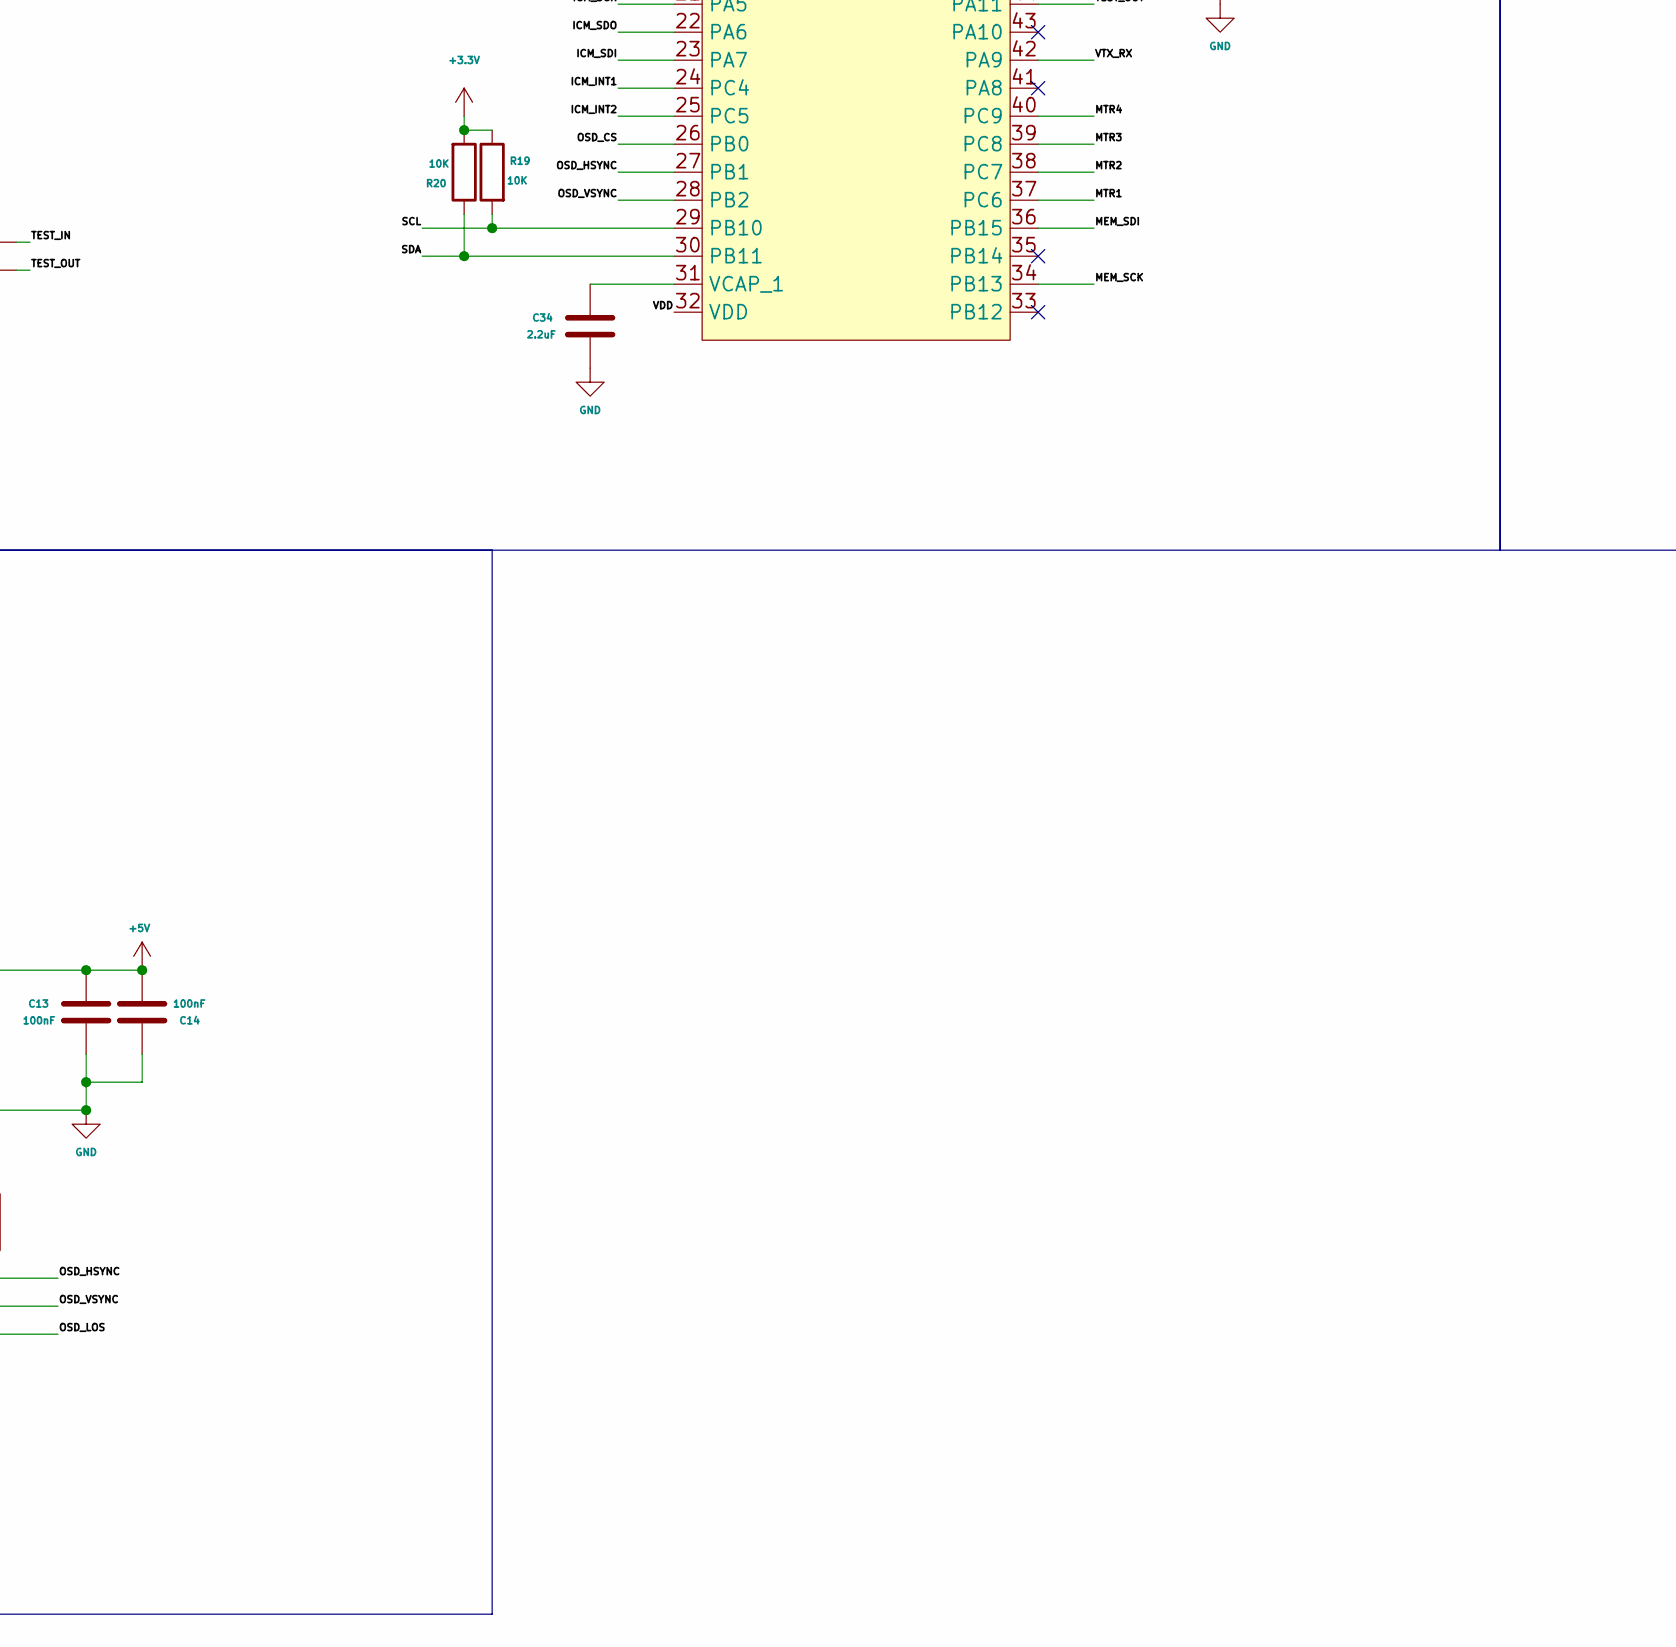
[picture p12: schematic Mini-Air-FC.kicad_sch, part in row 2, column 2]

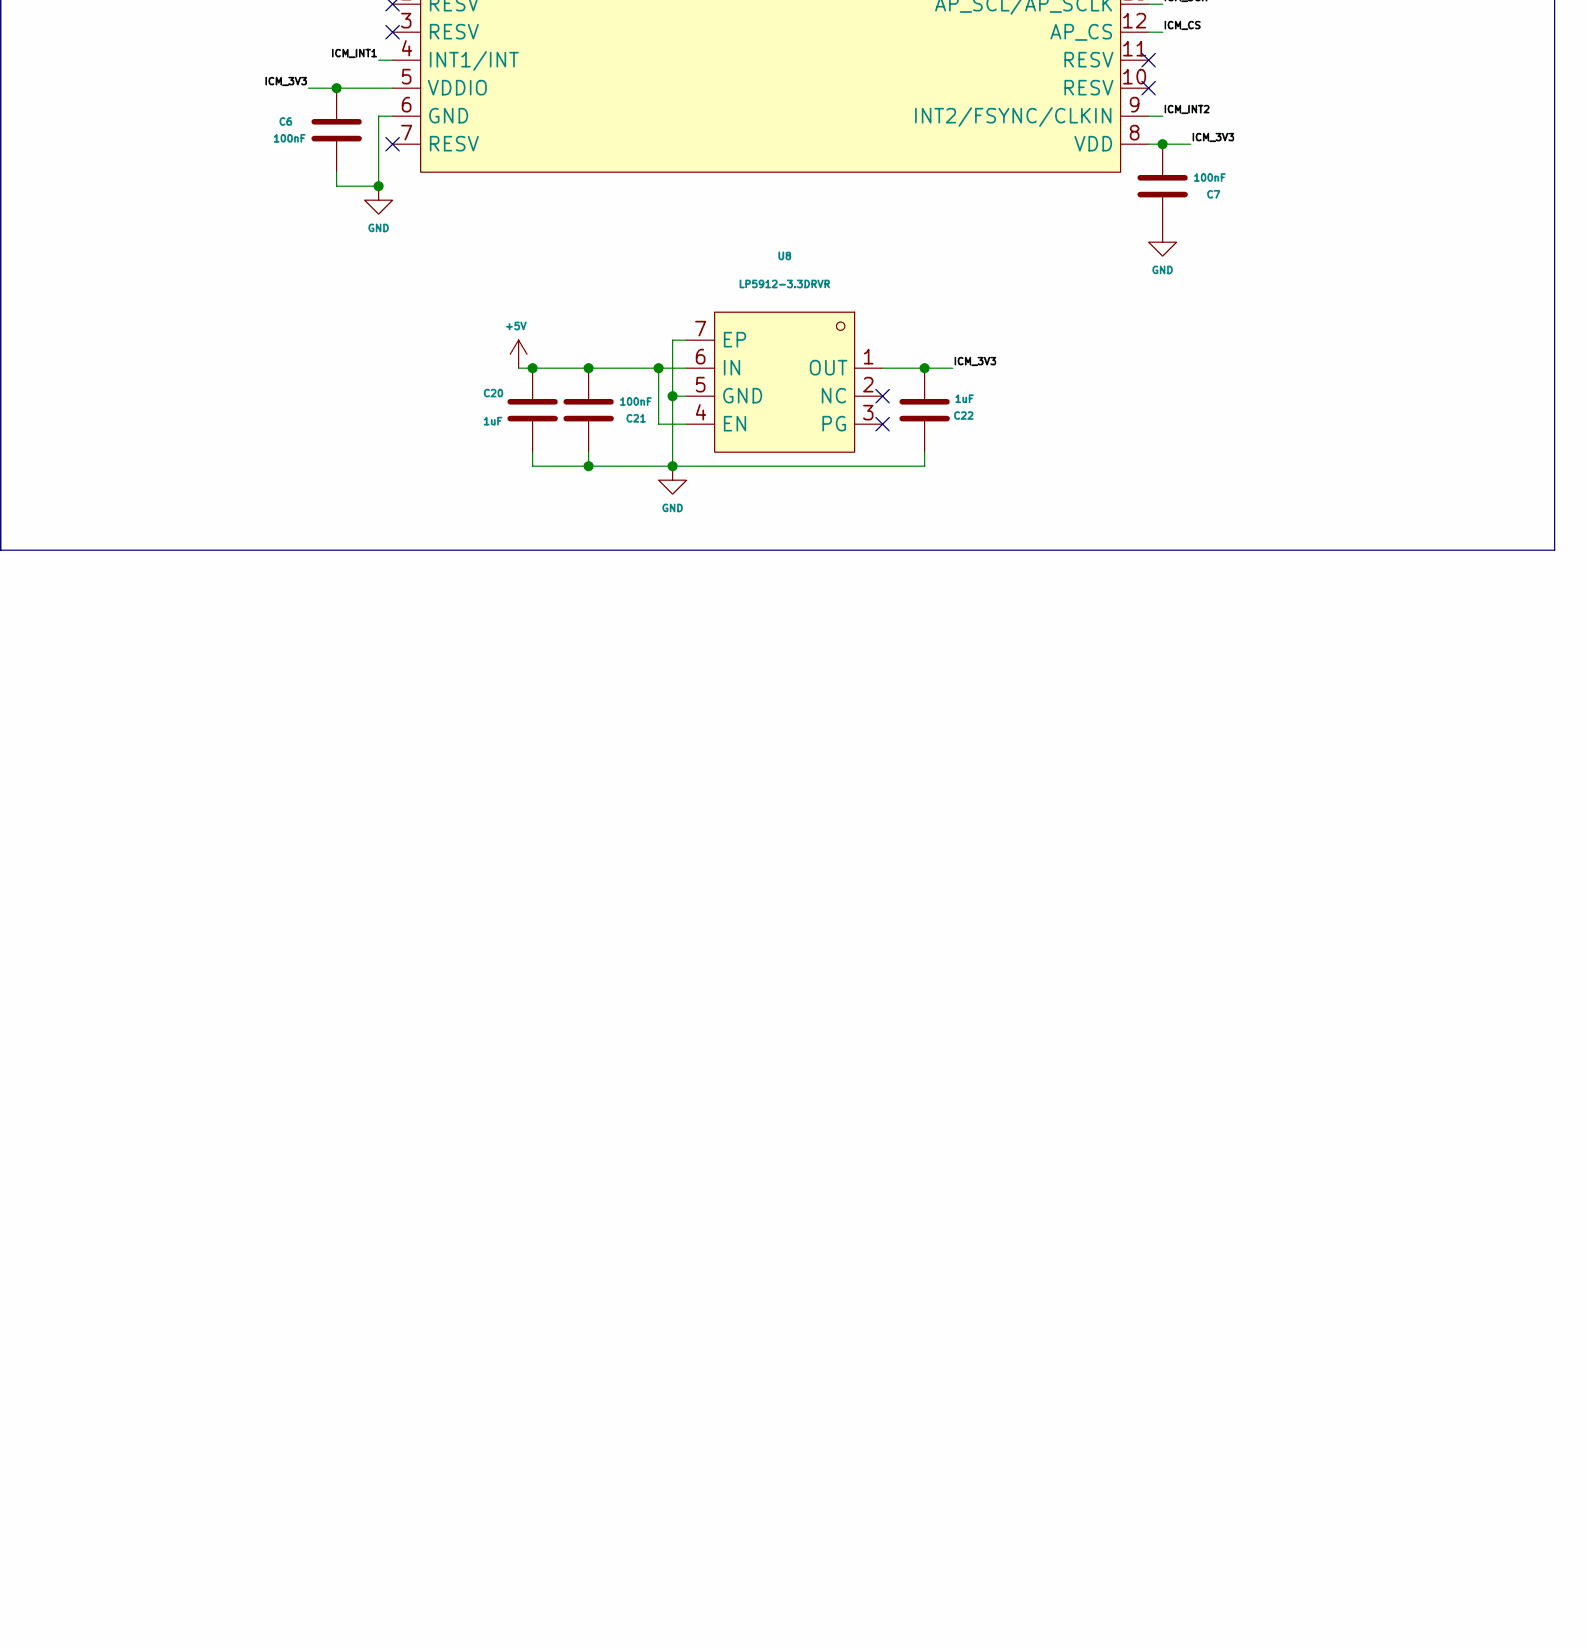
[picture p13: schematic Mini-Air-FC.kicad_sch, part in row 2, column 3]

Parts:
C2, C3, C15, C16: 22uF; C_0805_2012Metric
C4, C5, C20, C22, C26, C45, C46, C47: 1uF; C_0402_1005Metric
C6, C7, C8, C9, C10, C11, C12, C13, C14, C17, C21, C24, C27, C29, C36, C37, C38, C39, C40, C41, C42: 100nF; C_0201_0603Metric
C18, C19: 22pF; C_0201_0603Metric
C30, C31: 18pF; C_0201_0603Metric
C34, C35: 2.2uF; C_0402_1005Metric
C48: 10uF; C_0805_2012Metric
D1, D2, D3, D4: LED; LED_0402_1005Metric
J1, J9, J10: Conn_01x02; PinHeader_1x02_P1.00mm_Vertical
J2: Conn_01x08; JST_SH_SM08B-SRSS-TB_1x08-1MP_P1.00mm_Horizontal
J3, J5: Conn_01x06; PinHeader_1x06_P1.00mm_Vertical
J7, J11: Conn_01x04; PinHeader_1x04_P1.00mm_Vertical
J8: Conn_01x03; PinHeader_1x03_P1.00mm_Vertical
L1: FCM1608KF-601T03; L0603; MPN FCM1608KF-601T03; LCSC Part C141723
R4, R17, R18, R19, R20: 10K; R_0201_0603Metric
R5: 1.37K; R_0201_0603Metric
R6, R7, R8, R9: 500; R_0201_0603Metric
R10, R11: 75; R_0201_0603Metric
R12, R22: 100K; R_0201_0603Metric
R13, R14, R15: 1K; R_0201_0603Metric
R21, R23: 47K; R_0201_0603Metric
SW2: TS24CA; SW-SMD_2P-TS24CA; MPN TS24CA; LCSC Part C393942
U1: BMP280; LGA-8_L2.5-W2.0-P0.65_AMP6127; MPN BMP280; LCSC Part C83291
U2: ICM-42688-P; LGA-14_L3.0-W2.5-P0.50-TL; MPN ICM-42688-P; LCSC Part C1850418
U3, U8: LP5912-3.3DRVR; WSON-6_L2.0-W2.0-P0.65-TL-EP; MPN LP5912-3.3DRVR; LCSC Part C524780
U4: STM32F405RGT6TR; LQFP-64_L10.0-W10.0-P0.50-LS12.0-BL; MPN STM32F405RGT6TR; LCSC Part C2054141
U5: TPSM84209RKHT; QFN-9_L4.4-W4.0-P0.85-YTL; MPN TPSM84209RKHT; LCSC Part C2836944
U6: AT7456E; TSSOP-28_L9.7-W4.4-P0.65-LS6.4-BL-EP-2; MPN AT7456E; LCSC Part C82351
U7: W25Q128JVPIQ; WSON-8_L6.0-W5.0-P1.27-BL-EP; MPN W25Q128JVPIQ; LCSC Part C190862
X1: X322527MSB4SI; CRYSTAL-SMD_4P-L3.2-W2.5-BL-1; MPN X322527MSB4SI; LCSC Part C9008
X3: DSX321G 8MHz; CRYSTAL-SMD_4P-L3.2-W2.5-BL-1; MPN 1C208000BC0R; LCSC Part C57131

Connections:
+3.3V: C5.2, C8.1, C9.2, C26.1, C27.1, C36.2, C37.2, C38.2, C39.2, C40.2, C41.2, C45.2, C46.2, C47.2, C48.2, J3.1, L1.1, R6.1, R17.2, R18.1, R19.1, R20.2, U1.2 (CSB), U1.6 (VDDIO), U1.8 (VDD), U3.1 (OUT), U4.1 (VBAT), U4.19 (VDD), U4.32 (VDD), U4.48 (VDD), U4.64 (VDD), U7.8 (VCC)
+5V: C2.1, C4.1, C10.1, C12.2, C13.1, C14.2, C20.1, C21.2, J5.4, J7.3, J8.3, J11.1, R4.1, R13.1, R14.1, R15.1, U3.4 (EN), U3.6 (IN), U5.3 (VOUT), U6.3 (DVDD), U6.19 (~RESET), U6.21 (AVDD), U6.24 (PVDD), U8.4 (EN), U8.6 (IN)
+BATT: C3.2, C11.1, J1.2, U5.2 (VIN)
/ADC_C_ESC: C42.2, R22.2, R23.1, U4.16 (PA2)
/ADC_V_ESC: C24.2, R12.2, R21.1, U4.15 (PA1)
/BOOT0: C29.1, SW2.1, U4.60 (BOOT0)
/CAM_CTRL: J9.2, U4.11 (PC3)
/CAM_VID: C17.2, J8.1, R11.1
/C_ESC: J2.7, R22.1
/GPS_RX: J5.2, U4.14 (PA0_WKUP)
/GPS_TX: J5.1, U4.52 (PC11)
/HSE_IN: C30.1, U4.5 (PH0), X3.1 (OSC1)
/HSE_OUT: C31.2, U4.6 (PH1), X3.3 (OSC2)
/ICM_3V3: C6.1, C7.2, C22.2, U2.5 (VDDIO), U2.8 (VDD), U8.1 (OUT)
/ICM_CS: U2.12 (AP_CS), U4.20 (PA4)
/ICM_INT1: U2.4 (INT1/INT), U4.24 (PC4)
/ICM_INT2: U2.9 (INT2/FSYNC/CLKIN), U4.25 (PC5)
/ICM_SCK: U2.13 (AP_SCL/AP_SCLK), U4.21 (PA5)
/ICM_SDI: U2.14 (AP_SDA/AP_SDIO/AP_SDI), U4.23 (PA7)
/ICM_SDO: U2.1 (AP_SDO/AP_AD0), U4.22 (PA6)
/LED1: R7.2, U4.4 (PC15)
/LED2: R8.2, U4.3 (PC14)
/LED3: R9.2, U4.2 (PC13)
/MEM_CS: U4.9 (PC1), U7.1 (#CS)
/MEM_SCK: U4.34 (PB13), U7.6 (CLK)
/MEM_SDI: U4.36 (PB15), U7.5 (DI/IO0)
/MEM_SDO: U4.10 (PC2), U7.2 (DO/IO1)
/MTR1: J2.3, U4.37 (PC6)
/MTR2: J2.4, U4.38 (PC7)
/MTR3: J2.5, U4.39 (PC8)
/MTR4: J2.6, U4.40 (PC9)
/NRST: J3.5, U4.7 (NRST)
/OSD_CS: U4.26 (PB0), U6.8 (~CS)
/OSD_HSYNC: R13.2, U4.27 (PB1), U6.18 (~HSYNC)
/OSD_LOS: R15.2, U4.17 (PA3), U6.12 (LOS)
/OSD_SCK: U4.51 (PC10), U6.10 (SCLK)
/OSD_SDI: U4.57 (PB5), U6.9 (SDIN)
/OSD_SDO: U4.56 (PB4), U6.11 (SDOUT)
/OSD_VID: J11.3, R10.1
/OSD_VSYNC: R14.2, U4.28 (PB2), U6.17 (~VSYNC)
/RECEIVER_RX: J7.1, U4.53 (PC12)
/RECEIVER_TX: J7.2, U4.54 (PD2)
/SCL: J5.5, R19.2, U1.4 (SCK), U4.29 (PB10)
/SDA: J5.6, R20.1, U1.3 (SDI), U4.30 (PB11)
/SWCLK: J3.2, U4.49 (PA14)
/SWDIO: J3.4, U4.46 (PA13)
/SWO: J3.6, U4.55 (PB3)
/TEST_IN: J10.2, U4.45 (PA12)
/TEST_OUT: J10.1, U4.44 (PA11)
/VTX_RX: J11.4, U4.42 (PA9)
/V_ESC: J2.2, R12.1
GND: C2.2, C3.1, C4.2, C5.1, C6.2, C7.1, C8.2, C9.1, C10.2, C11.2, C12.1, C13.2, C14.1, C18.2, C19.2, C20.2, C21.1, C22.1, C24.1, C26.2, C27.2, C29.2, C30.2, C31.1, C34.2, C35.1, C36.1, C37.1, C38.1, C39.1, C40.1, C41.1, C42.1, C45.1, C46.1, C47.1, C48.1, D1.1 (K), D2.1 (K), D3.1 (K), D4.1 (K), J1.1, J2.1, J3.3, J5.3, J7.4, J8.2, J9.1, J11.2, R5.2, R11.2, R21.2, R23.2, SW2.2, U1.1 (GND), U1.5 (SDO), U1.7 (GND), U2.6 (GND), U3.5 (GND), U3.7 (EP), U4.12 (VSSA), U4.18 (VSS), U4.63 (VSS), U5.8 (GND), U6.4 (DGND), U6.20 (AGND), U6.23 (PGND), U6.29 (EP), U7.4 (GND), U7.9 (EP), U8.5 (GND), U8.7 (EP), X1.2 (GND), X1.4 (GND), X3.2 (NC), X3.4 (NC)
unnamed: C15.2, C16.1, R10.2
unnamed: D1.2 (A), R6.2
unnamed: D2.2 (A), R7.1
unnamed: D3.2 (A), R8.1
unnamed: D4.2 (A), R9.1
unnamed: C34.1, U4.31 (VCAP_1)
unnamed: C35.2, U4.47 (VCAP_2)
unnamed: L1.2, U4.13 (VDDA)
unnamed: R4.2, R5.1, U5.1 (FB)
unnamed: C19.1, U6.5 (CLKIN), X1.3 (OSC2)
unnamed: C15.1, U6.25 (SAG)
unnamed: C17.1, U6.22 (VIN)
unnamed: C16.2, U6.26 (VOUT)
unnamed: C18.1, U6.6 (XFB), X1.1 (OSC1)
unnamed: R17.1, U7.7 (#HOLD-OR-#REST/IO3)
unnamed: R18.2, U7.3 (#WP/IO2)

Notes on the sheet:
IMU
SPI Memory
ESC
Camera
Barometer
GPS
VTX
MCU
LEDs
OSD
Power Sensing
Battery, 5V Buck, 3v3 LDO
STLINK
Receiver

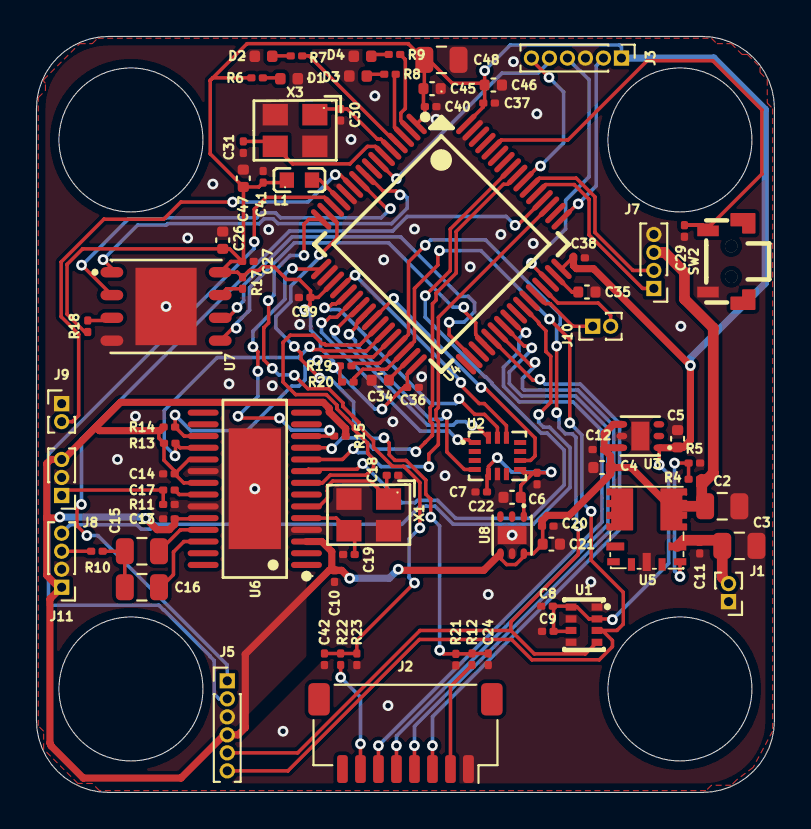
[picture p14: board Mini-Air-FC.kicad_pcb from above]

Board: 2 copper layers, 41.0 x 42.0 mm, 84 parts (0 on the bottom side), 68 nets.

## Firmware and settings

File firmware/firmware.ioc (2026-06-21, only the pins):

Mcu.UserName=STM32F405RGTx
PA0-WKUP.GPIO_Label=GPS_RX
PA0-WKUP.Signal=UART4_TX
PA1.GPIO_Label=ADC_V_ESC
PA1.Signal=ADCx_IN1
PA10.Signal=USART1_RX
PA11.GPIO_Label=TEST_OUT
PA11.Signal=GPIO_Output
PA12.GPIO_Label=TEST_IN
PA12.Signal=GPIO_Input
PA13.GPIO_Label=SWDIO
PA13.Signal=SYS_JTMS-SWDIO
PA14.GPIO_Label=SWCLK
PA14.Signal=SYS_JTCK-SWCLK
PA2.GPIO_Label=ADC_C_ESC
PA2.Signal=ADCx_IN2
PA3.GPIO_Label=OSD_LOS
PA3.Signal=GPIO_Input
PA4.GPIO_Label=ICM_CS
PA4.Signal=GPIO_Output
PA5.GPIO_Label=ICM_SCK
PA5.Signal=SPI1_SCK
PA6.GPIO_Label=ICM_SDO
PA6.Signal=SPI1_MISO
PA7.GPIO_Label=ICM_SDI
PA7.Signal=SPI1_MOSI
PA9.GPIO_Label=VTX_RX
PA9.Signal=USART1_TX
PB0.GPIO_Label=OSD_CS
PB0.Signal=GPIO_Output
PB1.GPIO_Label=OSD_HSYNC
PB1.Signal=GPIO_Input
PB10.GPIO_Label=SCL
PB10.Signal=I2C2_SCL
PB11.GPIO_Label=SDA
PB11.Signal=I2C2_SDA
PB13.GPIO_Label=MEM_SCK
PB13.Signal=SPI2_SCK
PB15.GPIO_Label=MEM_SDI
PB15.Signal=SPI2_MOSI
PB2.GPIO_Label=OSD_VSYNC
PB2.Signal=GPIO_Input
PB3.GPIO_Label=SWO
PB3.Signal=SYS_JTDO-SWO
PB4.GPIO_Label=OSD_SDO
PB4.Signal=SPI3_MISO
PB5.GPIO_Label=OSD_SDI
PB5.Signal=SPI3_MOSI
PC1.GPIO_Label=MEM_CS
PC1.Signal=GPIO_Output
PC10.GPIO_Label=OSD_SCK
PC10.Signal=SPI3_SCK
PC11.GPIO_Label=GPS_TX
PC11.Signal=UART4_RX
PC12.GPIO_Label=RECEIVER_RX
PC12.Signal=UART5_TX
PC13-ANTI_TAMP.GPIO_Label=LED3
PC13-ANTI_TAMP.Signal=GPIO_Output
PC14-OSC32_IN.GPIO_Label=LED2
PC14-OSC32_IN.Signal=GPIO_Output
PC15-OSC32_OUT.GPIO_Label=LED1
PC15-OSC32_OUT.Signal=GPIO_Output
PC2.GPIO_Label=MEM_SDO
PC2.Signal=SPI2_MISO
PC3.GPIO_Label=CAM_CTRL
PC3.Signal=GPIO_Output
PC4.GPIO_Label=ICM_INT1
PC4.Signal=GPXTI4
PC5.GPIO_Label=ICM_INT2
PC5.Signal=GPXTI5
PC6.GPIO_Label=MTR1
PC6.Signal=S_TIM8_CH1
PC7.GPIO_Label=MTR2
PC7.Signal=S_TIM8_CH2
PC8.GPIO_Label=MTR3
PC8.Signal=S_TIM8_CH3
PC9.GPIO_Label=MTR4
PC9.Signal=S_TIM8_CH4
PD2.GPIO_Label=RECEIVER_TX
PD2.Signal=UART5_RX
PH0-OSC_IN.GPIO_Label=HSE_IN
PH0-OSC_IN.Signal=RCC_OSC_IN
PH1-OSC_OUT.GPIO_Label=HSE_OUT
PH1-OSC_OUT.Signal=RCC_OSC_OUT
